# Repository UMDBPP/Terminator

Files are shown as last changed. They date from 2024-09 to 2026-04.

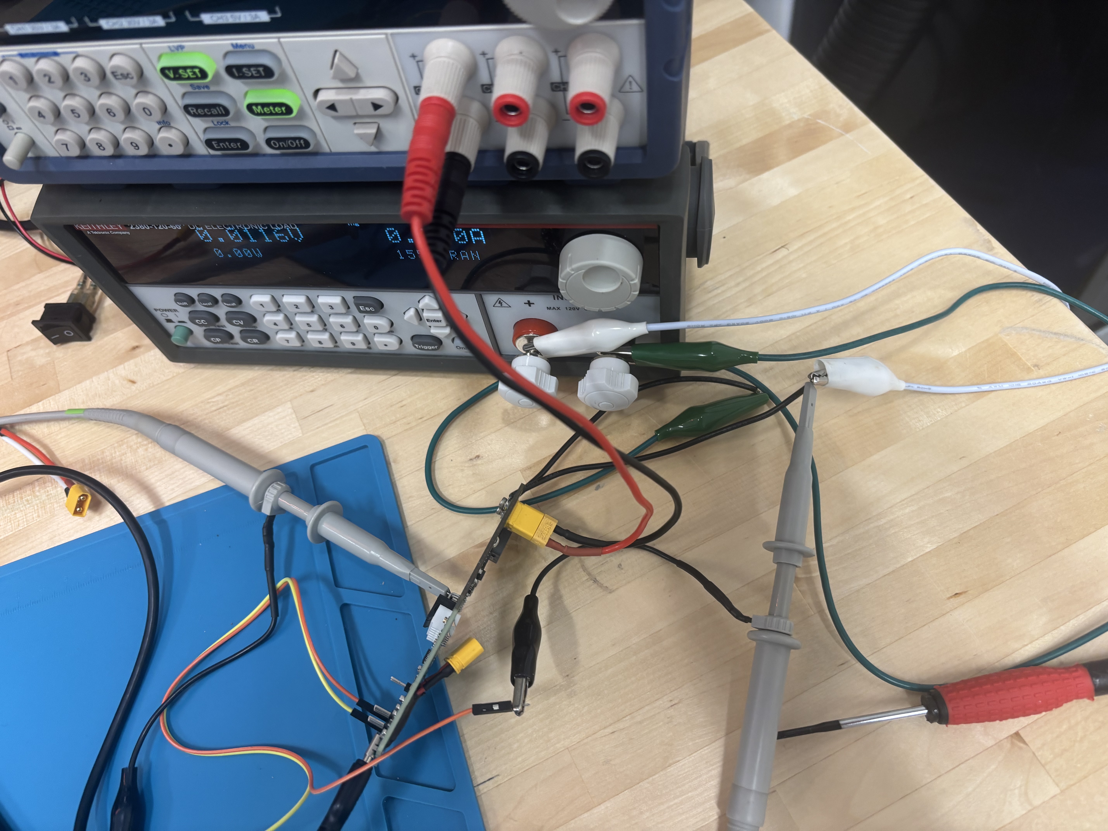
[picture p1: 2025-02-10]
Testing/T100x/TW_Load_Step/IMG_1361.jpeg

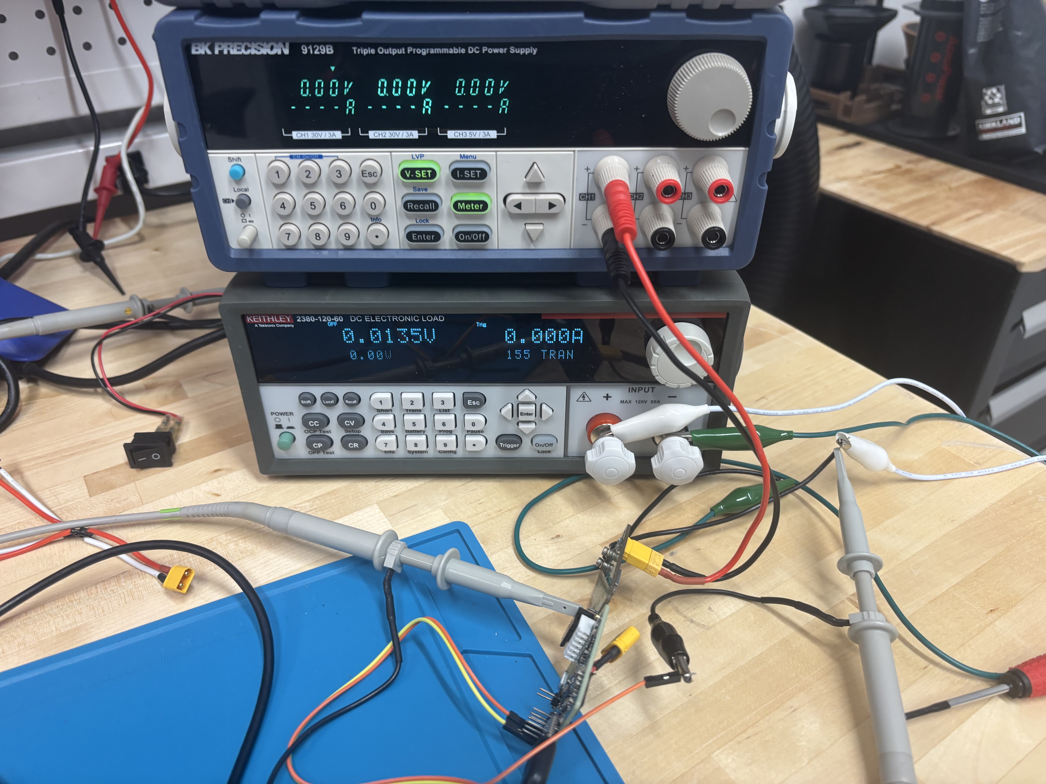
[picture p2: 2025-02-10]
Testing/T100x/TW_Load_Step/IMG_1360.jpeg

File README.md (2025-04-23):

# Terminator
A flight termination device for BPP.

## `T1100` - Current Revision

Much the same as T1000 but simpler and more complete.

## `T1000`
Shipman's ENEE499L project. The digital portion integrates a STM32L4, GPS, P/T Sensor, FRAM, and SX1262 Radio. This should provide quite a bit of flexibility in a small package while consuming minimal power. The digital board interfaces with a cutdown board which performs hot-wire termination like many other designs. However, this board is really just a barebones buck converter power stage that will be controlled by the digital board. This should provide increased flexiblity and efficiency over other implementations while also allowing T1000 to terminate even 550 paracord.

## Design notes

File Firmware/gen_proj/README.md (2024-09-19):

This project was originally generated by the STM32 Cube IDE. I just stole it and rippped it apart so I could build it myself and not be forced to use their IDE. Hopefully I'll also be able to steal some of their HAL functions too since I don't want to have to write them myself. The original project I used can be found in "empty_test_proj.zip"

# Project Structure
The structure of the project isn't too complicated.
- **build**: this fold contains the makefile and linker script used to build the final .elf file and other artifacts created during a build
- **src**: this contains source files that YOU write, things like main.c and other small or libraries
- **lib**: this is where you should put libraries you need to use for things like accessing I2C devices or parsing GPS data
- **vendor**: this includes code written by ARM and ST which perform basic configuration functions (e.g. the basic assembly run by the processor at startup that puts your application code in the right place in memory), unless you know what you are doing in here don't touch
    - **CMSIS**: this is the core stuff that configures the processor
    - **STM32L4_HAL**: this is hardware abstraction layer code written by ST, it should make things like using ADCs and configuring GPIOs easier, it is documented in ST UM1884 (google it)

## External Software Versions
ARM CMSIS, ST CMSIS, and the STM32 HAL found in the vendor directory are all external software provided by vendors. As described here: https://htmlpreview.github.io/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, they need to have the correct versions installed to function properly.

These version numbers are denoted by the release tags shown in Git or on the Github website and it's very easy to move between versions.

1. First check the versions you need by going to the link above and scrolling down to `Components > Drivers`
2. `cd` into `Terminator/Firmware/gen_proj/vendor/CMSIS`
3. List all available tags using `git tag`
4. Switch to the tag corresponding to the desired version number with `git checkout tags/<tag> -b <branch>`
    - Where `<tag>` is probably something like `5.6.0` and `<branch>` is probably `main`
5. Then confirm which tag you are on with `git describe --exact-match --tags`
6. Repeat steps 3-5 but first `cd Terminator/Firmware/gen_proj/vendor/CMSIS/Device/ST/STM32L4`
7. Repeat steps 3-5 but first `cd Terminator/Firmware/gen_proj/vendor/STM32L4_HAL`

# Building
The `build` folder is where the magic happens. The critical things it contains are: 

- **`makefile`**: contains the "recipe" for compiling code and creating an executable
- **`*.elf`**: the final executable, this is loaded onto a microcontroller and run
- **linker script**: a file that tells the linker where to put code in memory so that it will run properly

The TLDR steps for just building and flashing something are this:
1. `cd build` and run `make`
2. If you are connected to the MCU with an ST Link or some other programmer/debugger that is OpenOCD compatible, run `make flash`
3. If you are just connected over USB, but the device in USB DFU mode and flash the `.elf` file found in `build` to the device using the STM32 Programmer application

# References
Things I used to figure this out.
- ENEE440 - great class IMO, but I'm really into all this stuff so YMMV
- https://kleinembedded.com/stm32-without-cubeide-part-1-the-bare-necessities/
    - this really does explain most of it quite nicely, I had to figure some things out on my own to get this approach working with ST's provided startup and linker scripts
- https://vivonomicon.com/2018/04/02/bare-metal-stm32-programming-part-1-hello-arm/
- https://gist.github.com/maxtruxa/4b3929e118914ccef057f8a05c614b0f for the original Makefile

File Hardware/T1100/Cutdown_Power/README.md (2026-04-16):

Cutdown power stage for T1000 nichrome. [Click here to view in browser.](https://kicanvas.org/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)

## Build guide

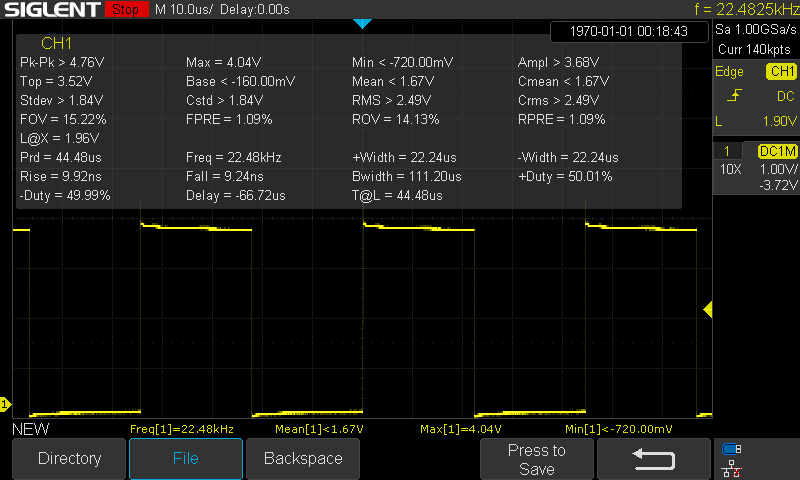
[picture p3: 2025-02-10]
Testing/T100x/TW_Load_Step/pid_loop_time.png

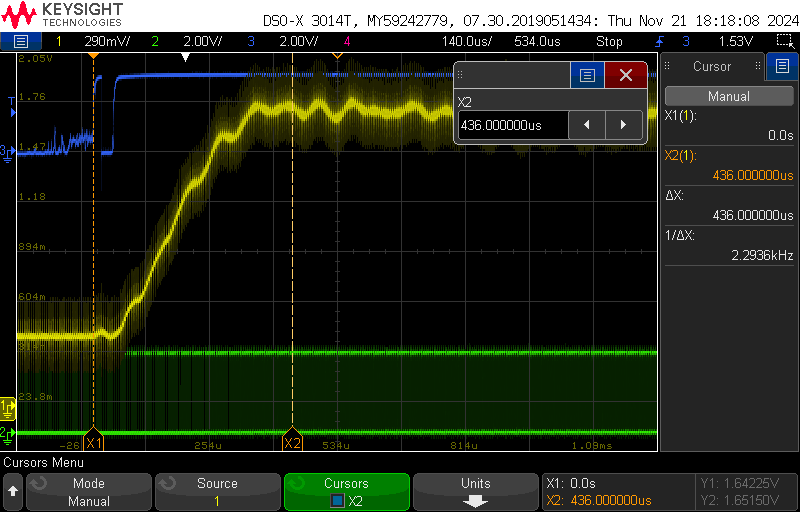
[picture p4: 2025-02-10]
Testing/T100x/TW_Load_Step/scope_4.png

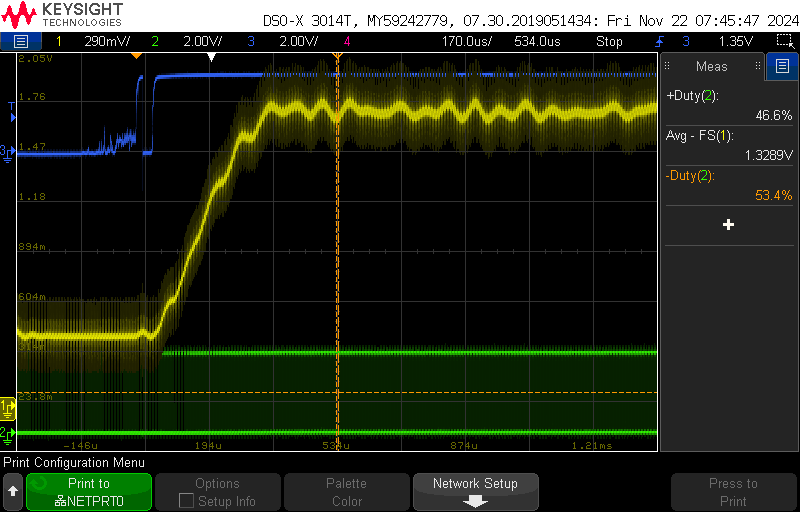
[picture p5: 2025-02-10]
Testing/T100x/TW_Load_Step/scope_0.png

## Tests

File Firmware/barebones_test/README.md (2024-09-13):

This directory is meant for developing the barebones components necessary to build a STM32 project from scratch. The two tutorials below have some good info. At some point I'd like to do this, but for now I can just copy a project generated by the STM32 Cube IDE and build it myself, which is easier since it generates all of the necessar boilerplate for me.

https://vivonomicon.com/2018/04/02/bare-metal-stm32-programming-part-1-hello-arm/
https://kleinembedded.com/stm32-without-cubeide-part-1-the-bare-necessities/

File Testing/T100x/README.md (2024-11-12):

# T100x Testing
A collection of data from testing T100x iterations. See the wiki development logs for more commentary.

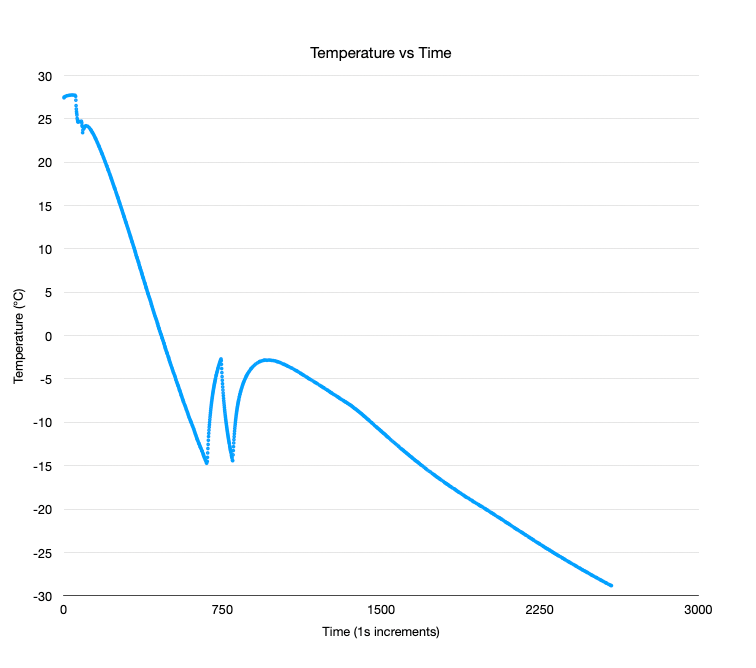
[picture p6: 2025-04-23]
Testing/T1100/T1100_board_heater_test_04212025.png

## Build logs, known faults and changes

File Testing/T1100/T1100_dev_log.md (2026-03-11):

# Board Heater

## Test 1

Ok so the little thermo-couple thermostat thing I chose works great. Turns on and off the NMOS FET perfectly and the long trace embeded in the board is very clearly able to heat it. The data in the 04/21/2025 graph shows that the heater brought the temp up from -15 C twice and then seemed to give up? That or it looks like it was just continuously on since the cooling happened much slower.

It only ran for ~43 minutes from what I can tell and restarted a lot once it reached about -28 C. The battery is also not very discharged so I'm not surprised that it didn't run very long. I'm going to re-run this test and log board temperature as well. My only other thought is that the battery got too cold for the amount of current the board heater draws so the system started dropping out. Not sure the best way to go about attaching the battery to the board since the back needs to be open for flight line to pass over.

Additionally since the system runs at 3.3V, maybe a 2S LiPo would be a better fit. Options are:
1. https://hobbyking.com/en_us/turnigy-nano-tech-300mah-2s-35c-lipo-pack-w-jst-ph-connector.html
2. https://hobbyking.com/en_us/turnigy-nano-tech-450mah-2s-65c-lipo-e-flite-compatible-blade-130x-eflb3002s35.html

## Test 2

This time also only ran for ~42 minutes which is odd to me, perhaps just a coincidence. This time I doubled the power through the heater and it worked much better before I'm pretty sure the battery voltage dropped to 3.3-3.4V and the regulator started having difficulties.

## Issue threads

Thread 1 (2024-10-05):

DIP Switch Pin out incorrect

michaelshipman, 2024-10-05:
Pin numbers and physical connections do not agree, currently bodging

michaelshipman, 2024-10-31:
Fixed on T1001

Closed 2024-10-31.

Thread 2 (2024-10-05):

GPS footprint pin 1 marking missing

michaelshipman, 2024-10-05:
need to add

Closed 2024-10-08.

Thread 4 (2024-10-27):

GPS Not working on battery power

michaelshipman, 2024-10-27:
For some reason the M10s have a VIO select option that either needs to be open or grounded depending on if 3.3v or 1.8v is used, either need to make system always use ~3v or implement some kind of solution

michaelshipman, 2024-10-31:
Fix for the moment is bumping the battery supplied regulator up to ~3.25v

michaelshipman, 2024-11-01:
New resistor values calculated, battery reg should be at a little under 3v once these come in.
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

Closed 2024-11-01.

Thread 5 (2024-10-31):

GPS returning incorrect coordinates and long lock time

michaelshipman, 2024-10-31:
Will have to put in actual numbers later but the coordinates from the receiver are pretty wrong, still in Maryland but probably 30ish miles away. UTC time is correct though.

I'm not sure why this is the case given that it was working a week or two ago.

Coupled with this issue is 20+ minute lock times for position.

I think my best bet right now is to reseat the GPS receiver, maybe over the last few weeks and a launch a solder joint or two have partially failed.

michaelshipman, 2024-11-01:
Replaced the MIA (from rev 0 build) and the antenna (new) and left running for a bit on the picnic table outside of MFG, not sure how long but I don't think more than 15 minutes.

Got time again but nothing else.

michaelshipman, 2024-11-01:
Going to put the RTC crystal on, RTC_O is supposed to be grounded when not used so I wonder if it's causing EMI issues

michaelshipman, 2024-11-01:
also the trace width was 0.22mm and JLC says it should be 0.1565, kicad calculator says 0.2

michaelshipman, 2024-11-01:
Viewing the spectrum, it's not the worst I've seen but not like the nice pretty one in the ublox manual. I'm not sure what the spikes are for one thing. It seems like a decently well formed spectrum and considering I'm in my apartment next to the window the received signal strength doesn't seem unrealistic.

**For future reference: the UBX-MON-SPAN is in View > Messages > Scroll down to Mon**

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

michaelshipman, 2024-11-01:
Oh also GPS baud for the MIA is 38400

michaelshipman, 2024-11-12:
I revved the board to T1002 to tune up the GPS section, have not assembled or tested yet but tuned the antenna line impedance and improved grounding

michaelshipman, 2024-11-14:
So I'm a bit of a dumb dumb, the NMEA lat long format confused me a little bit

This is what I got when the GPS did eventually get lock: 3859.55949,N,7656.33880,W

This is actually 38 + (59.55949 / 60) = 38.9926581667, and -76 + (56.33880 / 60) = -76.93898

Which is right on MFG actually

I still can't get it to lock consistently or quickly, but it does actually work when it does get position fix

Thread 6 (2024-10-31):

MS5607 I2C Inconsistent I2C comms

michaelshipman, 2024-10-31:
Some times data is just not being received. Unsure if this is a failure to wait for the device to fully convert/parse commands or something else. Tried lowering pull ups to 6.81k which didn't seem to help.

Sometimes data is returned though. Not entirely sure if it's correct data yet. May need to try and find a new one and see if this one is a dud.

Confident in the solder joints.

michaelshipman, 2024-11-12:
I added 20ms delays after transmitting commands and it's working nicely now. Have not tried to tune to shorter delay yet since it's not top priority before NS-130

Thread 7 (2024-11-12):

Re-assign exposed pins so USART TX/RX available on header

michaelshipman, 2024-11-12:
If possible try to re-assign exposed pins so that USART TX/RX can be used while cutdown power stage is attached. Can dump data over TX right now if re-assign PA2 which is used for power stage current sense.

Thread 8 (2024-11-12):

Power stage LVC/shutdown signal

michaelshipman, 2024-11-12:
The digital system should be able to power off the power stage board to save on power when not using it to cut. 1mA continuous draw adds up over the course of hours so being able to shut off the boost regulator on board would cut down on that.

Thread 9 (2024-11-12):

Move nichrome mount points on cutdown power stage

michaelshipman, 2024-11-12:
At the very least they need to be further apart to allow 550 paracord to fit between them.

More generally the physical layout of system needs to be improved since you can't package it the way I want to right now. This was partially intentional since the focus so far has been on designing something that could be tested and working with easily. But it means that it can't be packaged right now.

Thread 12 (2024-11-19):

GPS IO Voltage Switch

michaelshipman, 2024-11-19:
Need to select 1.8V or 3.3V on the MIA, added NMOS switched by OR controller that should solve this

Closed 2024-11-19.

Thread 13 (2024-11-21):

Interrupts not working on battery

michaelshipman, 2024-11-21:
I'm pretty sure this is the case for some reason, need to check on it again

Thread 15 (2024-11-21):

calculate LVC resistors for digital board reg

michaelshipman, 2024-11-21:
idk how I keep getting it wrong but it cuts off at 2.8V right now

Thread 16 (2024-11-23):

Swap STM32 HSE with a 32 MHz (or other) source

michaelshipman, 2024-11-23:
25 MHz doesn't divide evenly down to 48MHz which makes it impossible to use USB and have the core clock > the HSE source. 32 MHz or some other speed would be better, the TCXO used for the SX1262 should be pin to pin compatible with the current HSE, not sure if the footprint is close enough

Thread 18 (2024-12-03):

Potential Crosstalk on Digital Board

michaelshipman, 2024-12-03:
I haven't observed any issues but this was a silly oversight

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

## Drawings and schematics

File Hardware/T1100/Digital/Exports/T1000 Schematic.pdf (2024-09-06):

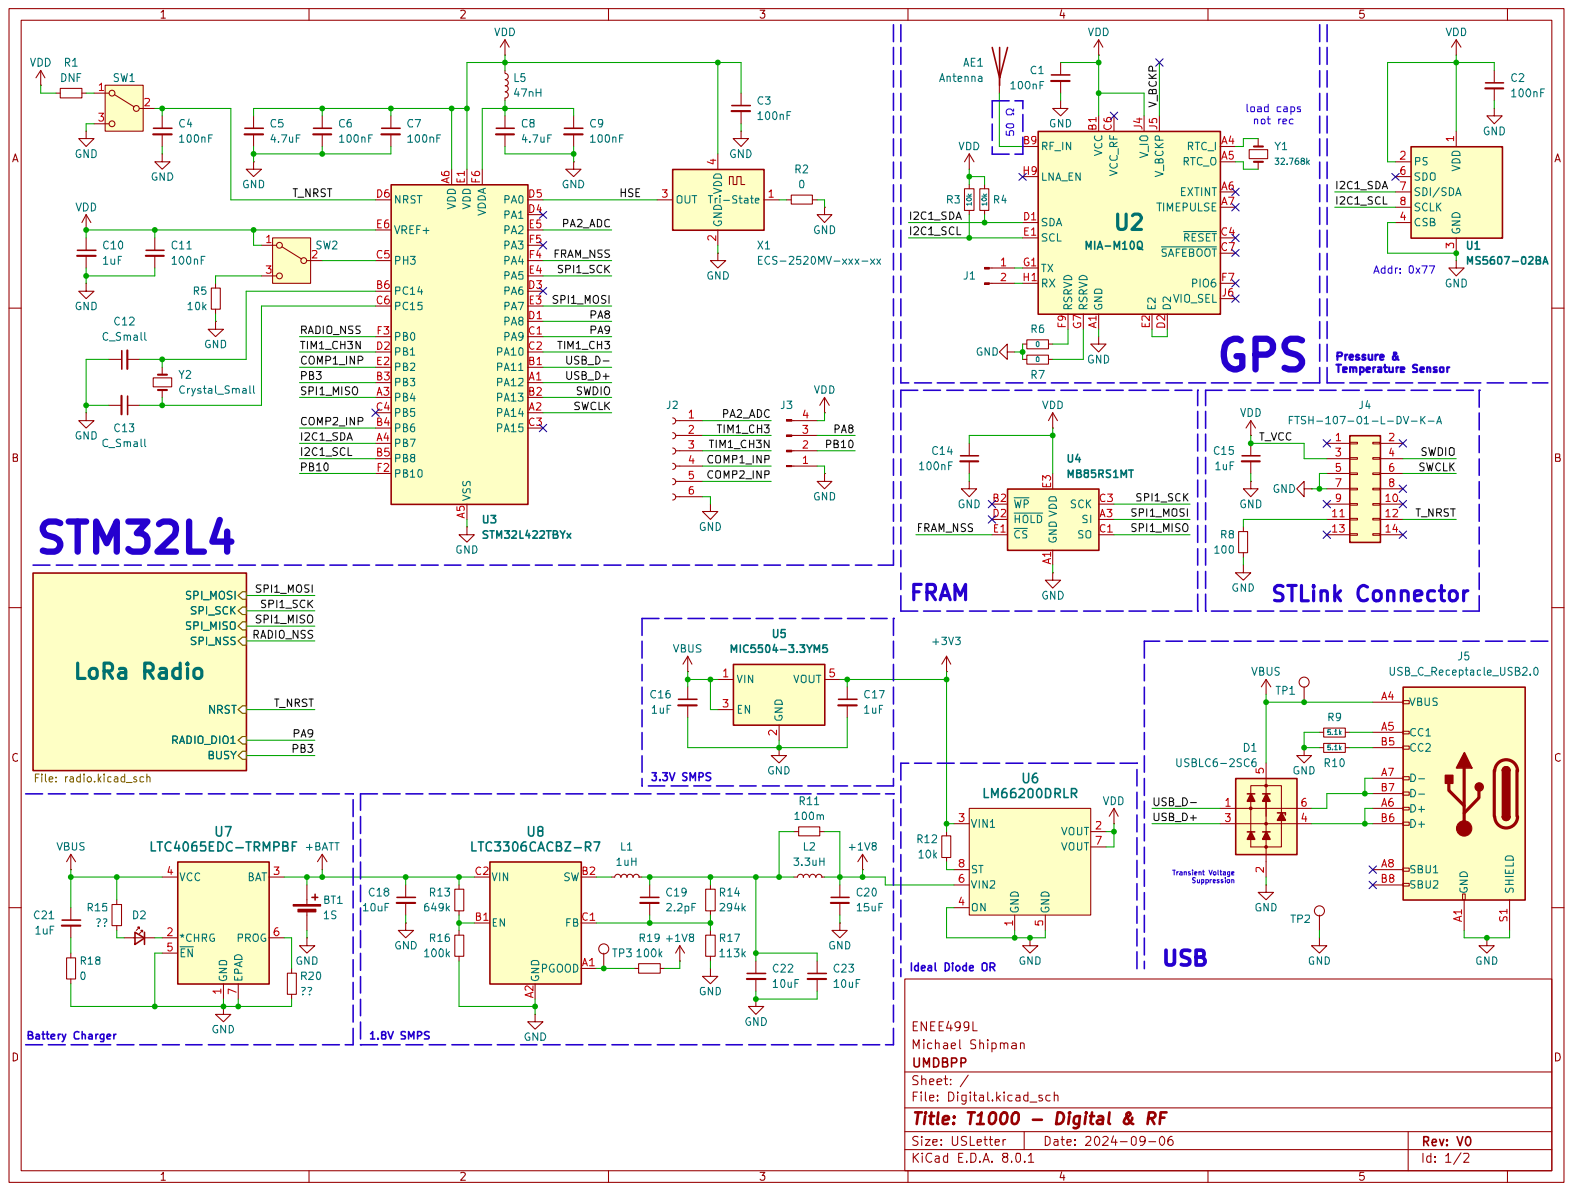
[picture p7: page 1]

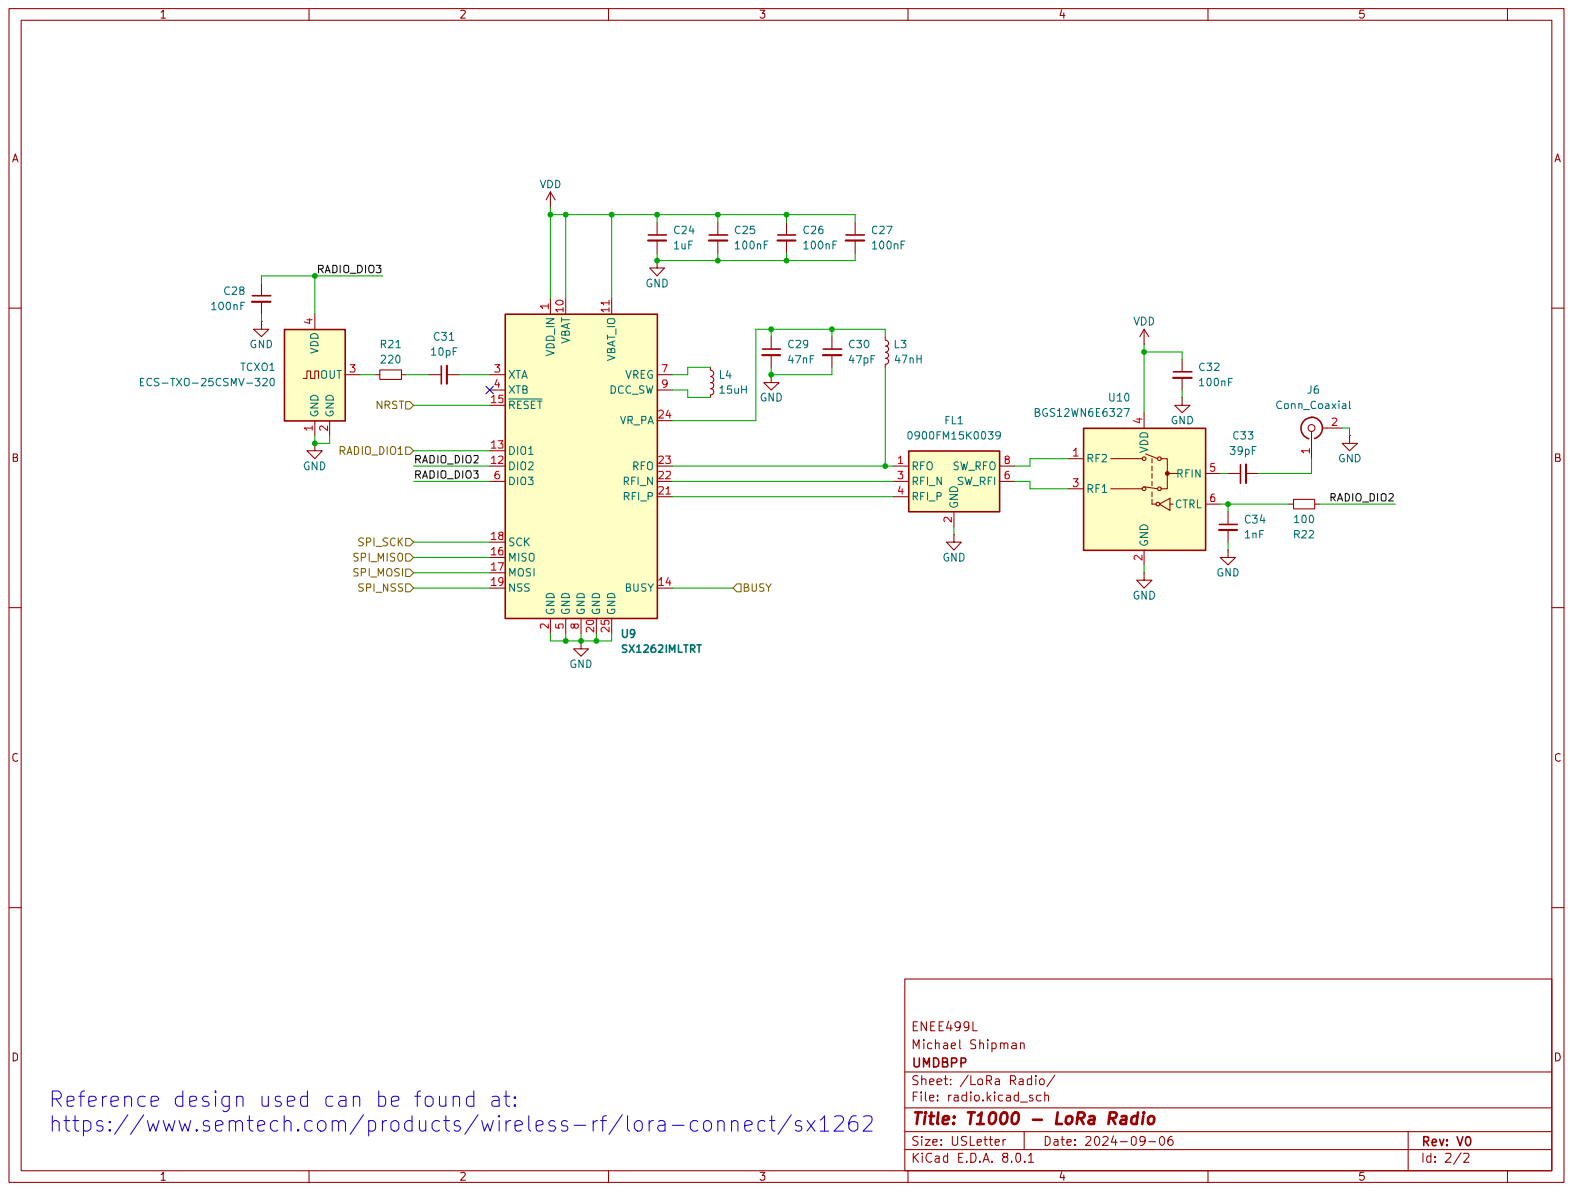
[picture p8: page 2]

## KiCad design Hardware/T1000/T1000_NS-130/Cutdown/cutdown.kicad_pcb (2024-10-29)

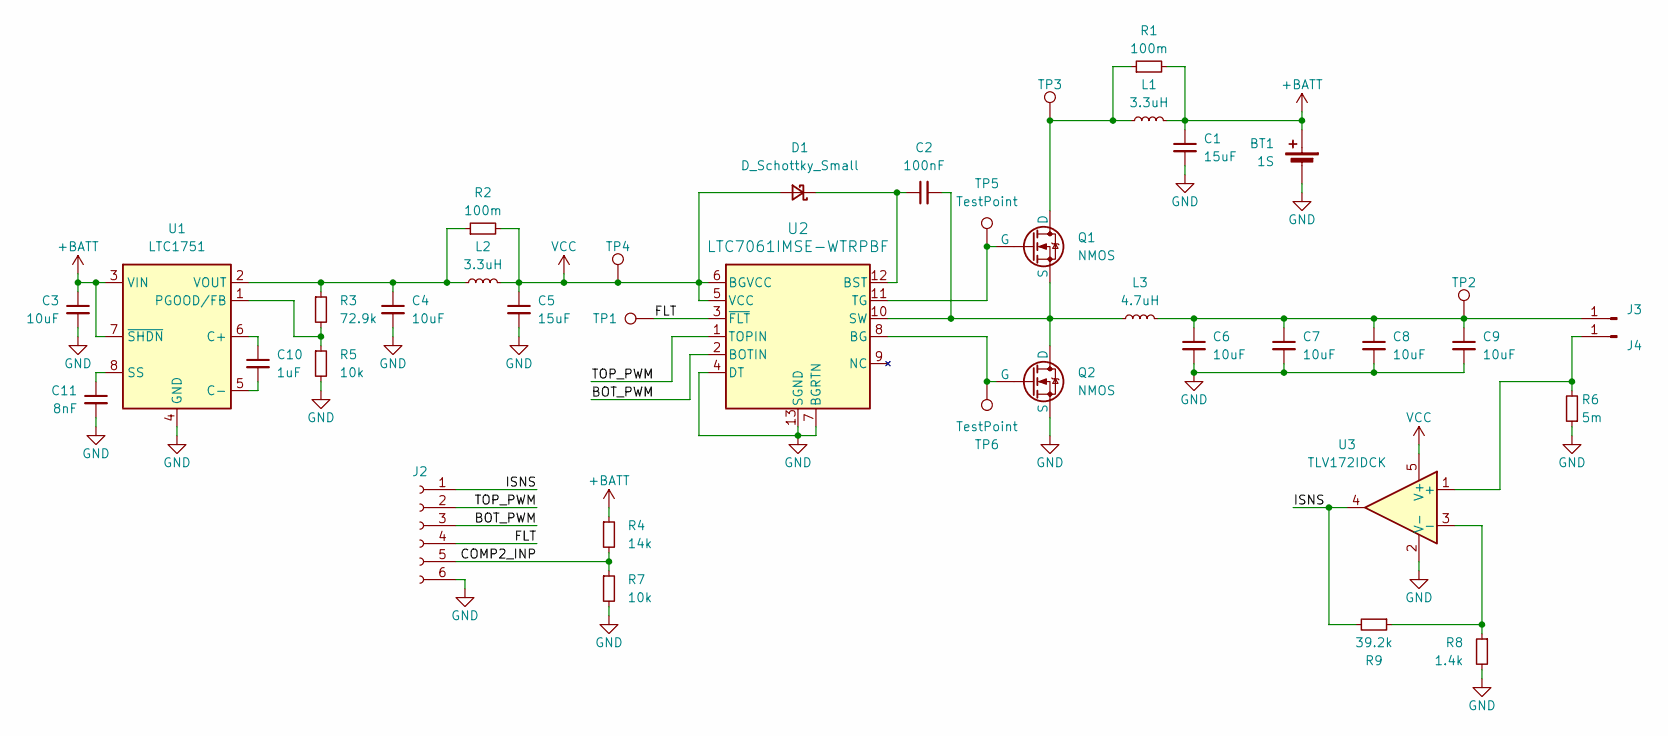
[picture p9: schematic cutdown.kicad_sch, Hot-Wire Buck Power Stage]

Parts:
BT1: 1S; AMASS_XT30U-F_1x02_P5.0mm_Vertical
C1, C5: 15uF; C_1206_3216Metric
C2: 100nF; C_0603_1608Metric
C3, C4: 10uF; C_0805_2012Metric
C6, C7, C8, C9: 10uF; C_1206_3216Metric
C10: 1uF; C_0603_1608Metric
C11: 8nF; C_0603_1608Metric
D1: D_Schottky_Small; D_SMA
J2: Conn_01x06_Socket; PinHeader_1x06_P2.54mm_Vertical
J3, J4: Conn_01x01_Pin; MountingHole_2.2mm_M2_DIN965_Pad
L1, L2: 3.3uH; L_1210_3225Metric
L3: 4.7uH; Wurth_74437368047
Q1, Q2: NMOS; CSD17307Q5A
R1, R2: 100m; C_0603_1608Metric
R3: 72.9k; R_0402_1005Metric
R4: 14k; R_0402_1005Metric
R5, R7: 10k; R_0402_1005Metric
R6: 5m; R_2512_6332Metric
R8: 1.4k; R_0603_1608Metric_Pad0.98x0.95mm_HandSolder
R9: 39.2k; R_0603_1608Metric_Pad0.98x0.95mm_HandSolder
TP1, TP2, TP3, TP4: TestPoint; TestPoint_Keystone_5000-5004_Miniature
TP5, TP6: TestPoint; TestPoint_Pad_D1.0mm
U1: LTC1751; MSOP-8_3x3mm_P0.65mm
U2: LTC7061IMSE-WTRPBF; MSOP-12-1EP_3x4mm_P0.65mm_EP1.65x2.85mm
U3: TLV172IDCK; SOT-353_SC-70-5

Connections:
+BATT: BT1.2 (+), C1.1, C3.1, L1.2, R1.2, R4.1, U1.3 (VIN), U1.7 (~SHDN)
/BOT_PWM: J2.3, U2.2 (BOTIN)
/COMP2_INP: J2.5, R4.2, R7.1
/FLT: J2.4, TP1.1, U2.3 (~FLT)
/ISNS: J2.1, R9.2, U3.4
/TOP_PWM: J2.2, U2.1 (TOPIN)
GND: BT1.1 (-), C1.2, C3.2, C4.2, C5.2, C6.2, C7.2, C8.2, C9.2, C11.2, J2.6, Q2.3 (S), R5.2, R6.1, R7.2, R8.2, U1.4 (GND), U2.4 (DT), U2.7 (BGRTN), U2.13 (SGND), U3.2 (V-)
unnamed: C2.1, D1.1 (K), U2.12 (BST)
unnamed: C6.1, C7.1, C8.1, C9.1, J3.1, L3.2, TP2.1
unnamed: J4.1, R6.2, U3.1 (+)
unnamed: L1.1, Q1.1 (D), R1.1, TP3.1
unnamed: Q1.2 (G), TP5.1, U2.11 (TG)
unnamed: C2.2, L3.1, Q1.3 (S), Q2.1 (D), U2.10 (SW)
unnamed: Q2.2 (G), TP6.1, U2.8 (BG)
unnamed: C10.1, U1.6 (C+)
unnamed: C10.2, U1.5 (C-)
unnamed: R3.2, R5.1, U1.1 (PGOOD/FB)
unnamed: C11.1, U1.8 (SS)
unnamed: C4.1, L2.1, R2.1, R3.1, U1.2 (VOUT)
unnamed: R8.1, R9.1, U3.3 (-)
VCC: C5.1, D1.2 (A), L2.2, R2.2, TP4.1, U2.5 (VCC), U2.6 (BGVCC), U3.5 (V+)

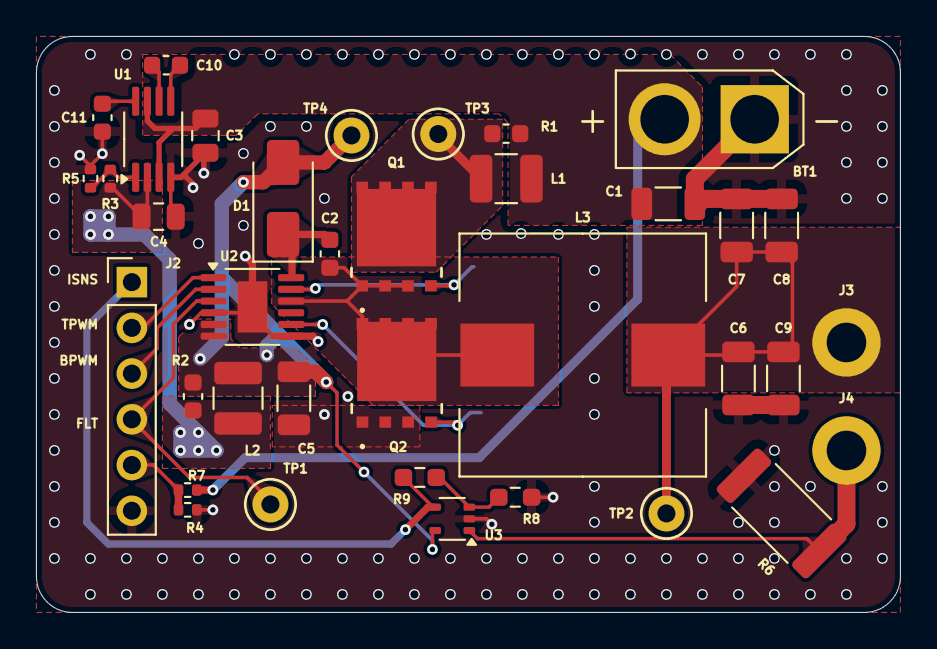
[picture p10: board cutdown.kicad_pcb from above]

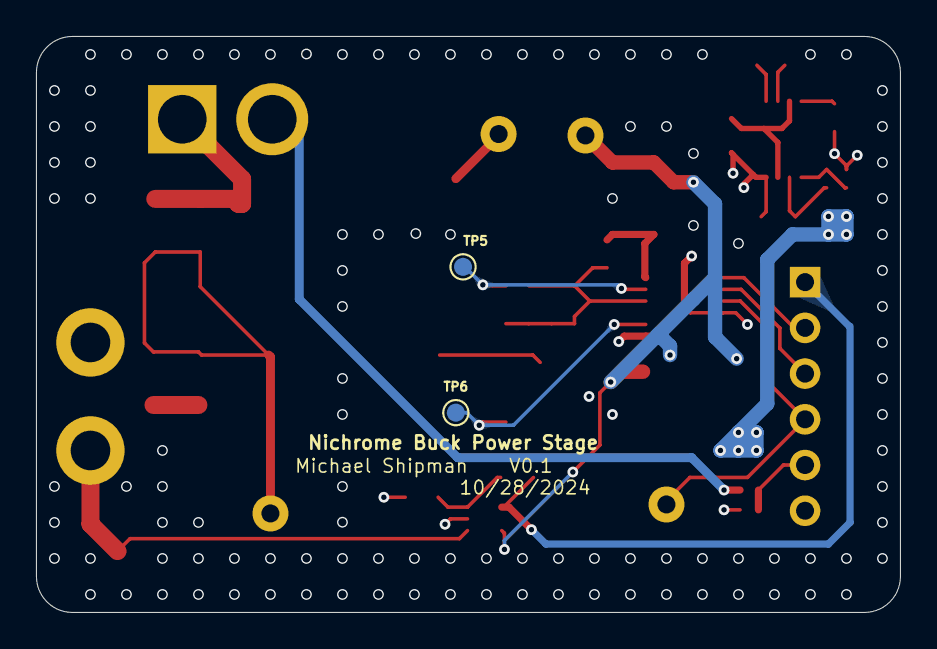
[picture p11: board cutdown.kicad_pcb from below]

Board: 4 copper layers, 48.0 x 32.0 mm, 39 parts (2 on the bottom side), 21 nets.

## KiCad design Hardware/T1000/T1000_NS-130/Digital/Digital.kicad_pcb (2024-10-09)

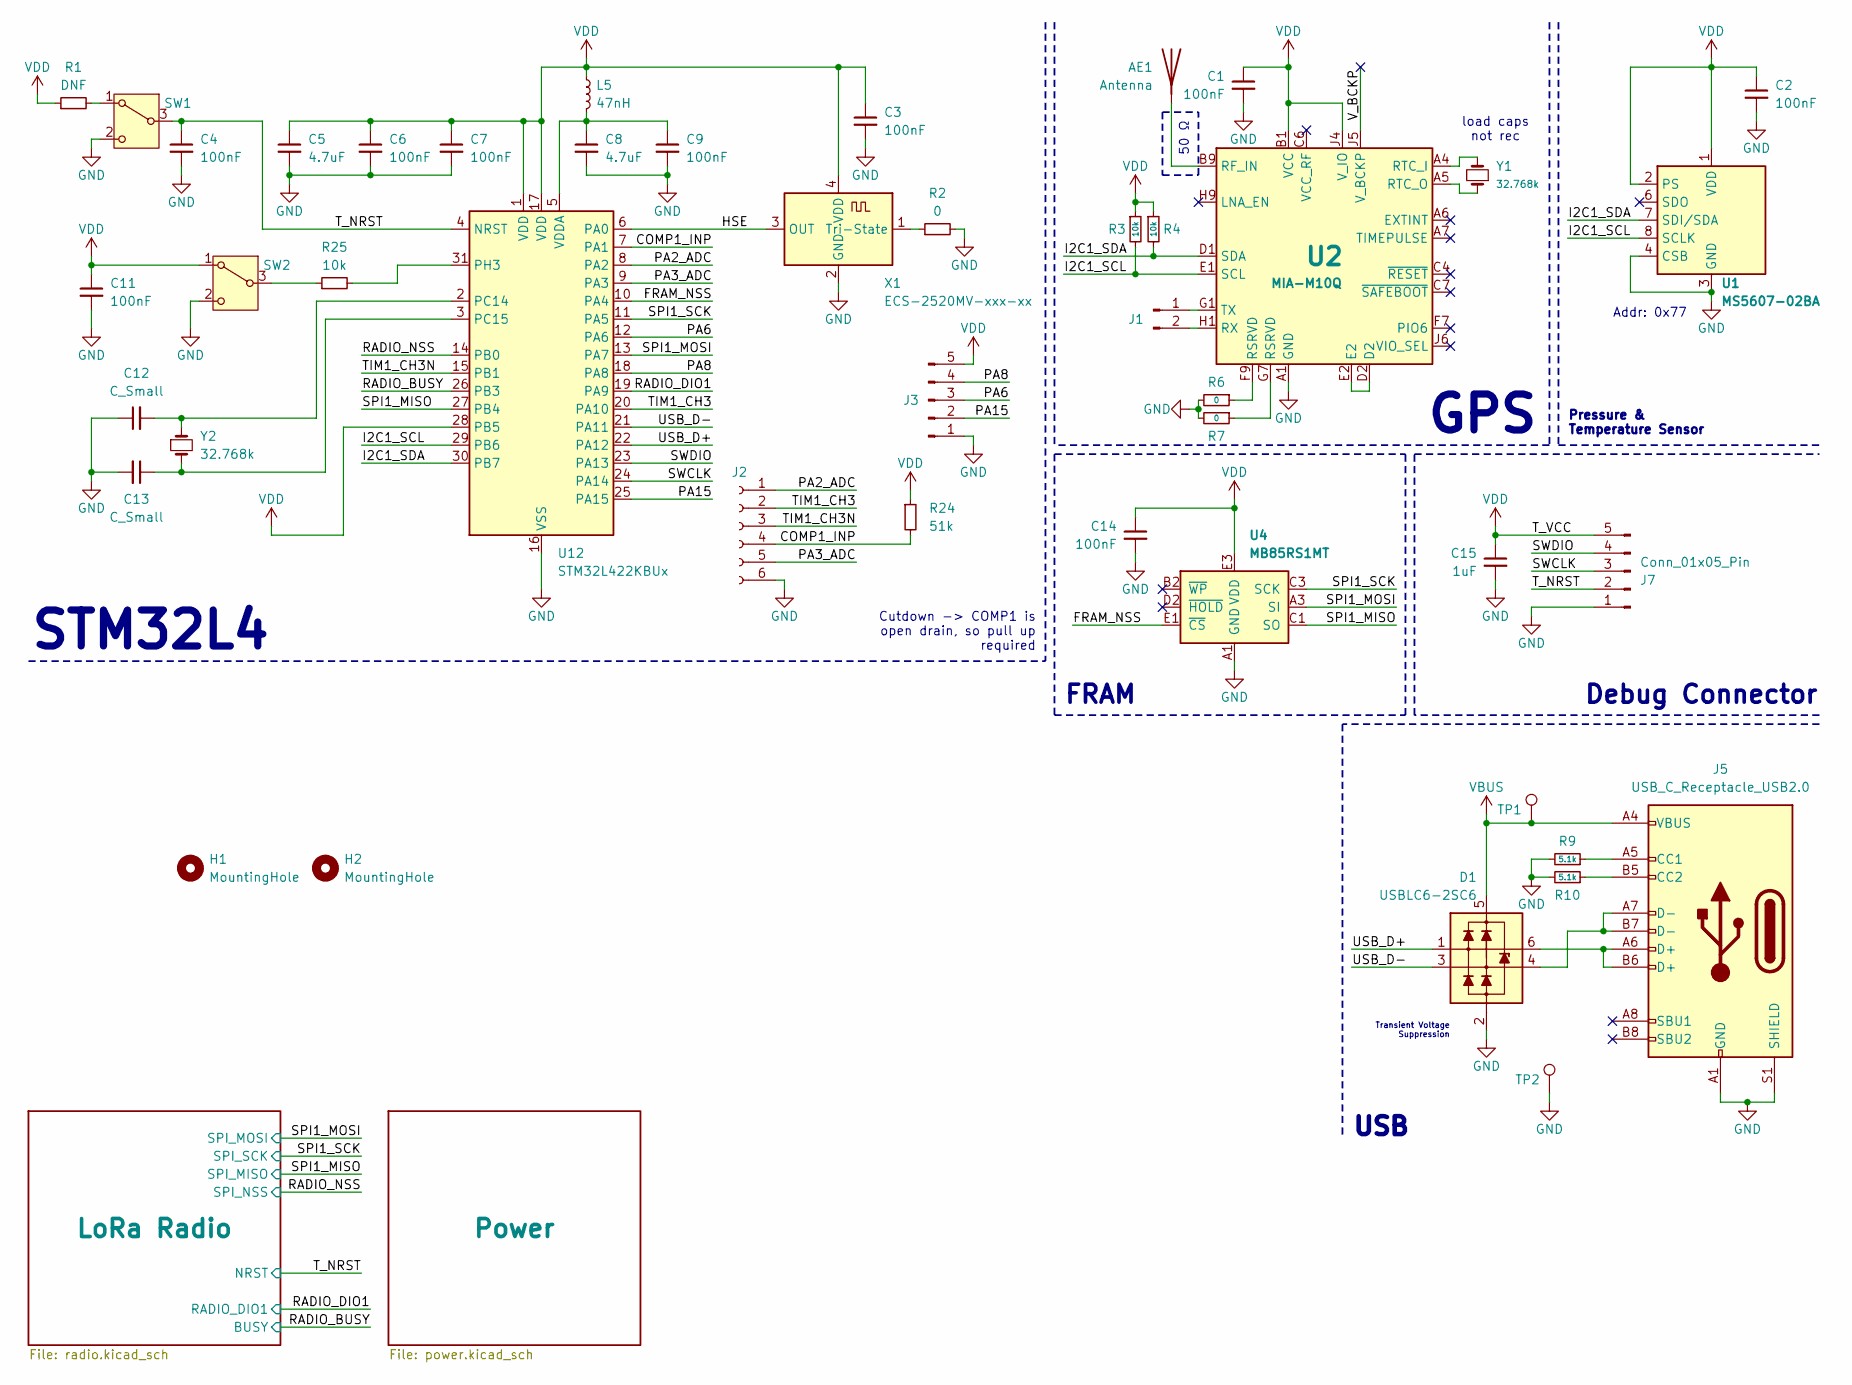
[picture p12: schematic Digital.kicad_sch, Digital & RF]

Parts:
AE1: Antenna; ANT_1575AT_JOT-M
C1, C2, C3, C4, C6, C7, C9, C11, C14: 100nF; C_0402_1005Metric
C5, C8: 4.7uF; C_0603_1608Metric
C12, C13: C_Small; C_0402_1005Metric
C15: 1uF; C_0603_1608Metric
D1: USBLC6-2SC6; TSOT-23-6
H1, H2: MountingHole; MountingHole_2.2mm_M2
J1: Conn_01x02_Pin; PinHeader_1x02_P2.54mm_Vertical
J2: Conn_01x06_Socket; PinHeader_1x06_P2.54mm_Vertical
J3, J7: Conn_01x05_Pin; PinHeader_1x05_P2.54mm_Vertical
J5: USB_C_Receptacle_USB2.0; USB_C_Receptacle_GCT_USB4105-xx-A_16P_TopMnt_Horizontal
L5: 47nH; L_0402_1005Metric
R1: DNF; R_0402_1005Metric
R2, R6, R7: 0; R_0402_1005Metric
R3, R4, R25: 10k; R_0402_1005Metric
R9, R10: 5.1k; R_0402_1005Metric
R24: 51k; R_0402_1005Metric
SW1, SW2: SW_SPDT; CAS-120TB_NDC-M
TP1, TP2: TestPoint; TestPoint_Pad_D1.0mm
U1: MS5607-02BA; LGA-8_3x5mm_P1.25mm
U2: MIA-M10Q
U4: MB85RS1MT; BGA8CP30X40_5X3_309X228X35B25N
U12: STM32L422KBUx; QFN-32-1EP_5x5mm_P0.5mm_EP3.45x3.45mm
X1: ECS-2520MV-xxx-xx; Oscillator_SMD_ECS_2520MV-xxx-xx-4Pin_2.5x2.0mm
Y1, Y2: 32.768k; Crystal_SMD_3215-2Pin_3.2x1.5mm

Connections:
/COMP1_INP: J2.4, R24.2, U12.7 (PA1)
/FRAM_NSS: U4.E1 (~CS), U12.10 (PA4)
/HSE: U12.6 (PA0), X1.3 (OUT)
/I2C1_SCL: R3.2, U1.8 (SCLK), U2.E1 (SCL), U12.29 (PB6)
/I2C1_SDA: R4.2, U1.7 (SDI/SDA), U2.D1 (SDA), U12.30 (PB7)
/PA2_ADC: J2.1, U12.8 (PA2)
/PA3_ADC: J2.5, U12.9 (PA3)
/PA6: J3.3, U12.12 (PA6)
/PA8: J3.4, U12.18 (PA8)
/PA15: J3.2, U12.25 (PA15)
/RADIO_BUSY: U12.26 (PB3); also elsewhere on the board
/RADIO_DIO1: U12.19 (PA9); also elsewhere on the board
/RADIO_NSS: U12.14 (PB0); also elsewhere on the board
/SPI1_MISO: U4.C1 (SO), U12.27 (PB4); also elsewhere on the board
/SPI1_MOSI: U4.A3 (SI), U12.13 (PA7); also elsewhere on the board
/SPI1_SCK: U4.C3 (SCK), U12.11 (PA5); also elsewhere on the board
/SWCLK: J7.3, U12.24 (PA14)
/SWDIO: J7.4, U12.23 (PA13)
/TIM1_CH3: J2.2, U12.20 (PA10)
/TIM1_CH3N: J2.3, U12.15 (PB1)
/T_NRST: C4.1, J7.2, SW1.3 (C), U12.4 (NRST); also elsewhere on the board
/USB_D+: D1.1 (L1), U12.22 (PA12)
/USB_D-: D1.3 (L2), U12.21 (PA11)
/V_BCKP: U2.J5 (V_BCKP)
GND: C1.2, C2.2, C3.2, C4.2, C5.2, C6.2, C7.2, C8.2, C9.2, C11.2, C12.1, C13.2, C14.2, C15.2, D1.2 (VN), J2.6, J3.1, J5.A1 (GND), J5.A12 (GND), J5.B1 (GND), J5.B12 (GND), J5.S1 (SHIELD), J7.1, R2.2, R6.2, R7.2, R9.2, R10.2, SW1.2 (B), SW2.2 (B), TP2.1, U1.3 (GND), U1.4 (CSB), U1.5 (CSB), U2.A1 (GND), U2.A2 (GND), U2.A3 (GND), U2.A8 (GND), U2.A9 (GND), U2.B2 (GND), U2.B8 (GND), U2.C3 (GND), U2.C9 (GND), U2.E3 (GND), U2.E4 (GND), U2.E9 (GND), U2.F1 (GND), U2.F3 (GND), U2.F4 (GND), U2.G3 (GND), U2.G4 (GND), U2.G5 (GND), U2.G6 (GND), U2.H8 (GND), U2.J8 (GND), U2.J9 (GND), U4.A1 (GND), U12.16 (VSS), U12.32 (VSS), U12.33 (VSS), X1.2 (GND); also elsewhere on the board
unnamed: AE1.1 (A), U2.B9 (RF_IN)
unnamed: D1.6 (L1), J5.A6 (D+), J5.B6 (D+)
unnamed: D1.4 (L2), J5.A7 (D-), J5.B7 (D-)
unnamed: J1.1, U2.G1 (TX)
unnamed: J1.2, U2.H1 (RX)
unnamed: J5.A5 (CC1), R9.1
unnamed: J5.B5 (CC2), R10.1
unnamed: R6.1, U2.F9 (RSRVD)
unnamed: R7.1, U2.G7 (RSRVD)
unnamed: R1.2, SW1.1 (A)
unnamed: R25.1, SW2.3 (C)
unnamed: U2.A4 (RTC_I), Y1.2
unnamed: U2.A5 (RTC_O), Y1.1
unnamed: C12.2, U12.2 (PC14), Y2.1
unnamed: C13.1, U12.3 (PC15), Y2.2
unnamed: R25.2, U12.31 (PH3)
unnamed: C8.1, C9.1, L5.2, U12.5 (VDDA)
unnamed: R2.1, X1.1 (Tri-State)
VBUS: D1.5 (VP), J5.A4 (VBUS), J5.A9 (VBUS), J5.B4 (VBUS), J5.B9 (VBUS), TP1.1; also elsewhere on the board
VDD: C1.1, C2.1, C3.1, C5.1, C6.1, C7.1, C11.1, C14.1, C15.1, J3.5, J7.5, L5.1, R1.1, R3.1, R4.1, R24.1, SW2.1 (A), U1.1 (VDD), U1.2 (PS), U2.B1 (VCC), U2.J4 (V_IO), U4.E3 (VDD), U12.1 (VDD), U12.17 (VDD), U12.28 (PB5), X1.4 (VDD); also elsewhere on the board

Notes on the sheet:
load caps not rec
GPS
Transient Voltage Suppression
Debug Connector
Cutdown -> COMP1 is open drain, so pull up required
FRAM
50 Ω
USB
Pressure & Temperature Sensor
STM32L4
Addr: 0x77

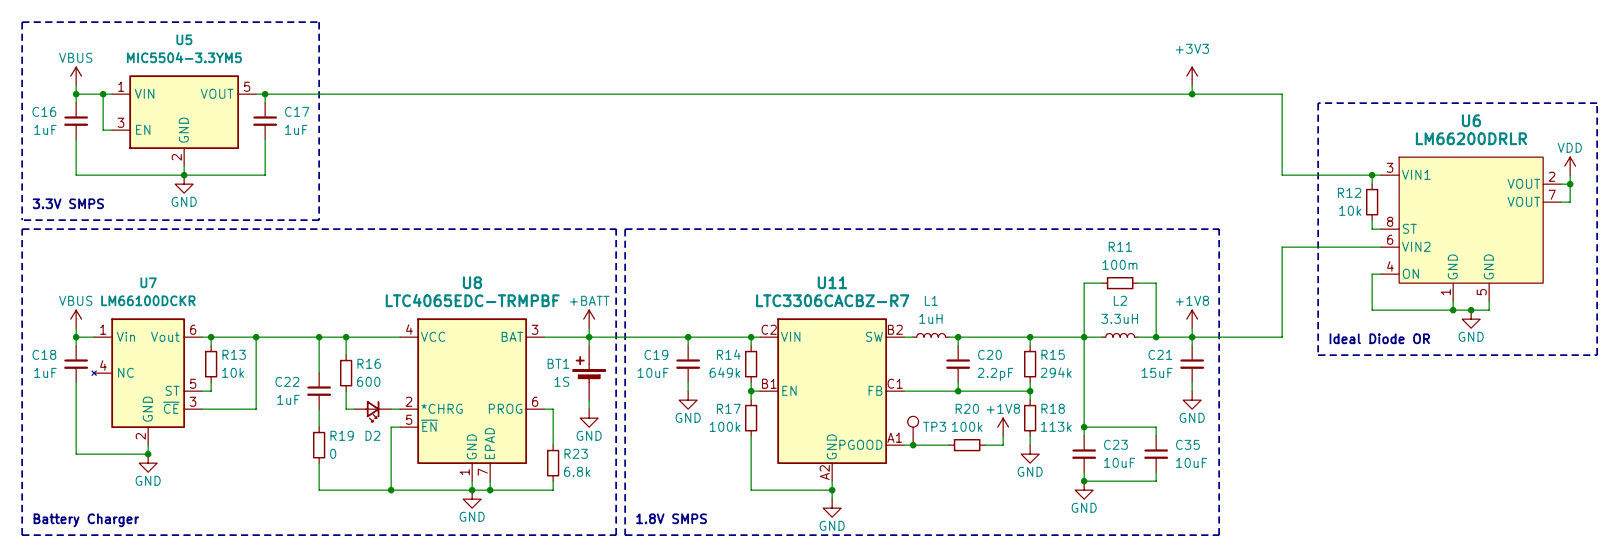
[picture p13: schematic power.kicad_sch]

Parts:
BT1: 1S; PinHeader_1x02_P2.54mm_Vertical
C16, C17, C18, C22: 1uF; C_0603_1608Metric
C19, C23, C35: 10uF; C_0805_2012Metric
C20: 2.2pF; C_0402_1005Metric
C21: 15uF; C_1206_3216Metric
D2: LED_Small; LED_0603_1608Metric
L1: 1uH; L_0805_2012Metric
L2: 3.3uH; L_1210_3225Metric
R11: 100m; R_0402_1005Metric
R12, R13: 10k; R_0402_1005Metric
R14: 649k; R_0402_1005Metric
R15: 294k; R_0402_1005Metric
R16: 600; R_0402_1005Metric
R17, R20: 100k; R_0402_1005Metric
R18: 113k; R_0402_1005Metric
R19: 0; R_0402_1005Metric
R23: 6.8k; R_0402_1005Metric
TP3: TestPoint; TestPoint_Pad_D1.0mm
U5: MIC5504-3.3YM5; SOT-23-5
U6: LM66200DRLR; SOT-5X3_DRL_TEX
U7: LM66100DCKR; SOT-363_SC-70-6
U8: LTC4065EDC-TRMPBF; DFN-6_DC_LIT
U11: LTC3306CACBZ-R7; CB-6-19_ADI

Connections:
+1V8: C21.1, L2.2, R11.2, R20.2, U6.6 (VIN2)
+3V3: C17.1, R12.1, U5.5 (VOUT), U6.3 (VIN1)
+BATT: BT1.1 (+), C19.1, R14.1, U8.3 (BAT), U11.C2 (VIN)
GND: BT1.2 (-), C16.2, C17.2, C18.2, C19.2, C21.2, C23.2, C35.2, R17.2, R18.2, R19.2, R23.2, U5.2 (GND), U6.1 (GND), U6.4 (ON), U6.5 (GND), U7.2 (GND), U8.1 (GND), U8.5 (~EN), U8.7 (EPAD), U11.A2 (GND); also elsewhere on the board
unnamed: C20.1, C23.1, C35.1, L1.2, L2.1, R11.1, R15.1
unnamed: C22.2, R19.1
unnamed: D2.2 (A), R16.2
unnamed: D2.1 (K), U8.2 (*CHRG)
unnamed: R12.2, U6.8 (ST)
unnamed: R13.2, U7.5 (ST)
unnamed: C22.1, R13.1, R16.1, U7.3 (~CE), U7.6 (Vout), U8.4 (VCC)
unnamed: R23.1, U8.6 (PROG)
unnamed: R14.2, R17.1, U11.B1 (EN)
unnamed: C20.2, R15.2, R18.1, U11.C1 (FB)
unnamed: R20.1, TP3.1, U11.A1 (PGOOD)
unnamed: L1.1, U11.B2 (SW)
VBUS: C16.1, C18.1, U5.1 (VIN), U5.3 (EN), U7.1 (Vin); also elsewhere on the board
VDD: U6.2 (VOUT), U6.7 (VOUT); also elsewhere on the board

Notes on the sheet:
Battery Charger
Ideal Diode OR
3.3V SMPS
1.8V SMPS

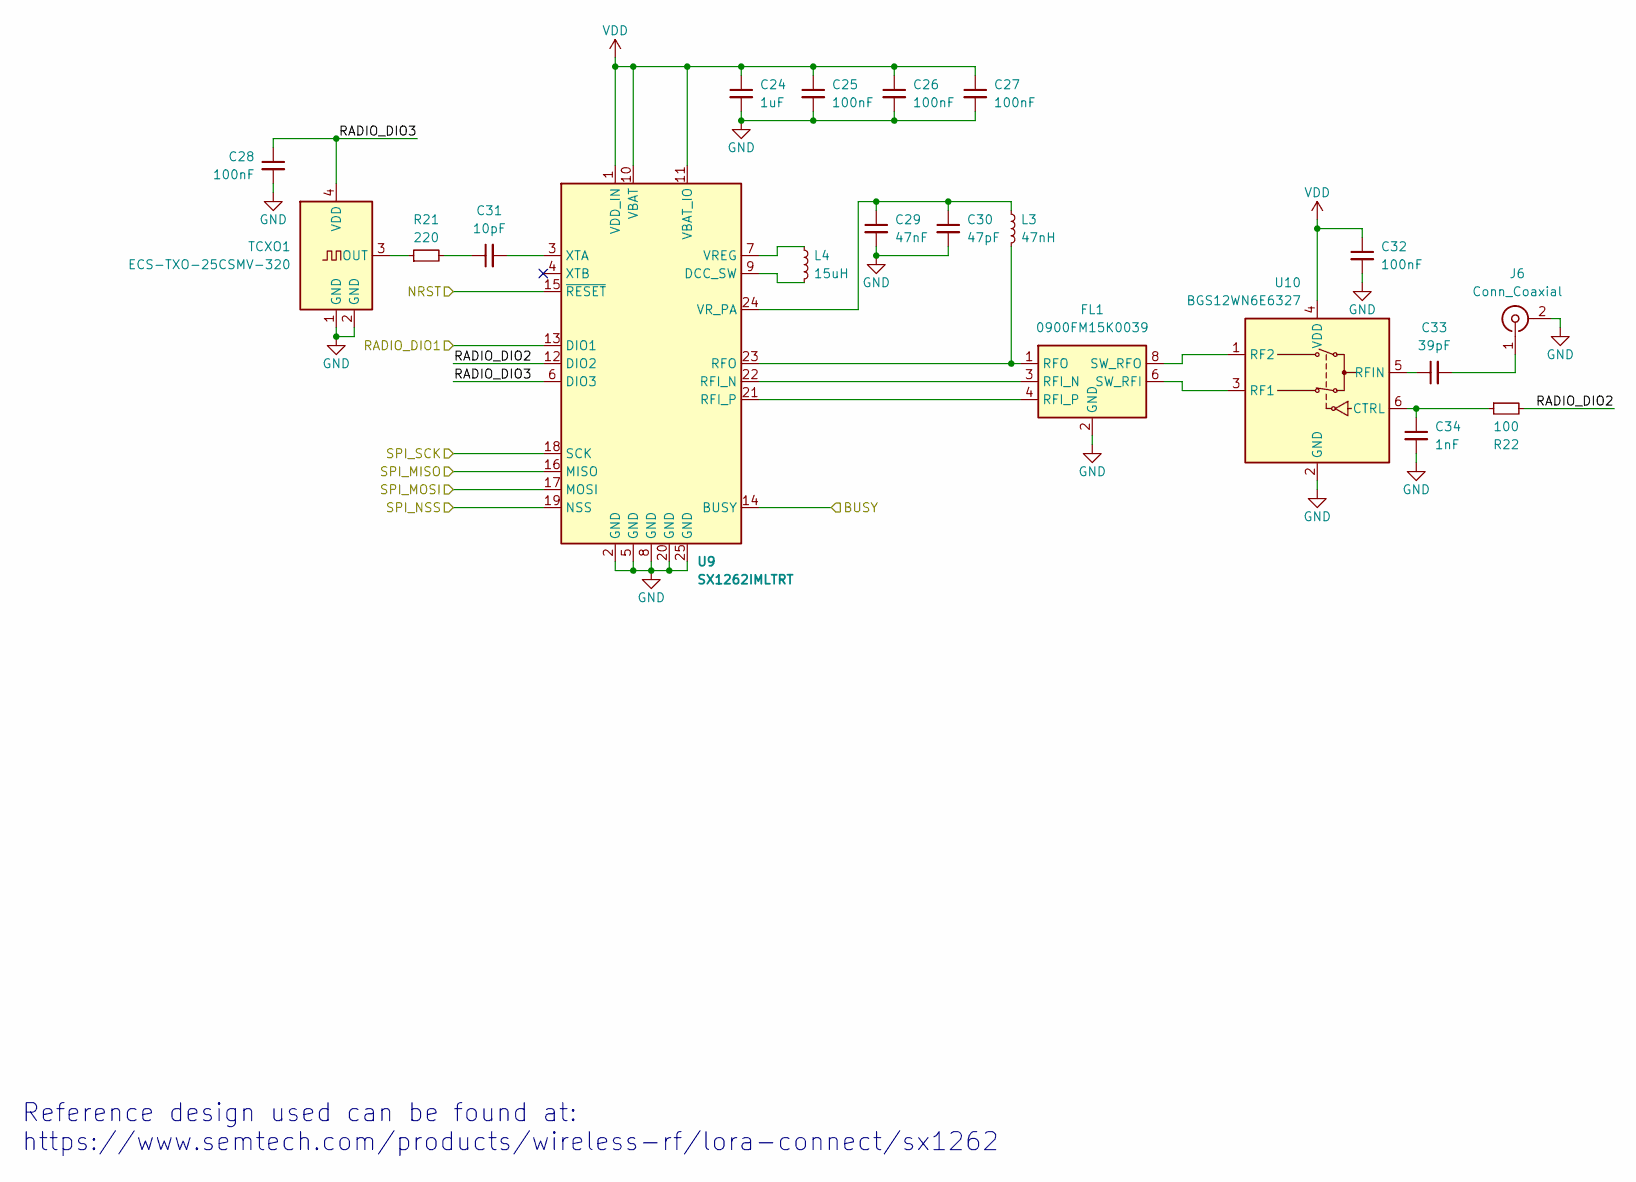
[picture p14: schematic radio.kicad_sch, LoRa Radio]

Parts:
C24: 1uF; C_0603_1608Metric
C25, C26, C27, C28, C32: 100nF; C_0402_1005Metric
C29: 47nF; C_0402_1005Metric
C30: 47pF; C_0402_1005Metric
C31: 10pF; C_0402_1005Metric
C33: 39pF; C_0402_1005Metric
C34: 1nF; C_0402_1005Metric
FL1: 0900FM15K0039; Balun_Johanson_0900FM15K0039
J6: Conn_Coaxial; U.FL_Molex_MCRF_73412-0110_Vertical
L3: 47nH; L_0402_1005Metric
L4: 15uH; L_0805_2012Metric
R21: 220; R_0402_1005Metric
R22: 100; R_0402_1005Metric
TCXO1: ECS-TXO-25CSMV-320; Crystal_SMD_2520-4Pin_2.5x2.0mm
U9: SX1262IMLTRT; QFN-24-1EP_4x4mm_P0.5mm_EP2.6x2.6mm
U10: BGS12WN6E6327; Infineon_PG-TSNP-6-10_0.7x1.1mm_0.7x1.1mm_P0.4mm

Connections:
/LoRa Radio/RADIO_DIO2: R22.2, U9.12 (DIO2)
/LoRa Radio/RADIO_DIO3: C28.1, TCXO1.4 (VDD), U9.6 (DIO3)
/RADIO_BUSY: U9.14 (BUSY); also elsewhere on the board
/RADIO_DIO1: U9.13 (DIO1); also elsewhere on the board
/RADIO_NSS: U9.19 (NSS); also elsewhere on the board
/SPI1_MISO: U9.16 (MISO); also elsewhere on the board
/SPI1_MOSI: U9.17 (MOSI); also elsewhere on the board
/SPI1_SCK: U9.18 (SCK); also elsewhere on the board
/T_NRST: U9.15 (~RESET); also elsewhere on the board
GND: C24.2, C25.2, C26.2, C27.2, C28.2, C29.2, C30.2, C32.2, C34.2, FL1.2 (GND), FL1.5 (GND), FL1.7 (GND), FL1.9 (GND), FL1.10 (GND), J6.2 (Ext), TCXO1.1 (GND), TCXO1.2 (GND), U9.2 (GND), U9.5 (GND), U9.8 (GND), U9.20 (GND), U9.25 (GND), U10.2 (GND); also elsewhere on the board
unnamed: C31.1, R21.2
unnamed: FL1.3 (RFI_N), U9.22 (RFI_N)
unnamed: FL1.4 (RFI_P), U9.21 (RFI_P)
unnamed: FL1.1 (RFO), L3.2, U9.23 (RFO)
unnamed: FL1.6 (SW_RFI), U10.3 (RF1)
unnamed: FL1.8 (SW_RFO), U10.1 (RF2)
unnamed: C33.2, J6.1 (In)
unnamed: R21.1, TCXO1.3 (OUT)
unnamed: L4.2, U9.9 (DCC_SW)
unnamed: L4.1, U9.7 (VREG)
unnamed: C29.1, C30.1, L3.1, U9.24 (VR_PA)
unnamed: C31.2, U9.3 (XTA)
unnamed: C34.1, R22.1, U10.6 (CTRL)
unnamed: C33.1, U10.5 (RFIN)
VDD: C24.1, C25.1, C26.1, C27.1, C32.1, U9.1 (VDD_IN), U9.10 (VBAT), U9.11 (VBAT_IO), U10.4 (VDD); also elsewhere on the board

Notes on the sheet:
Reference design used can be found at: https://www.semtech.com/products/wireless-rf/lora-connect/sx1262

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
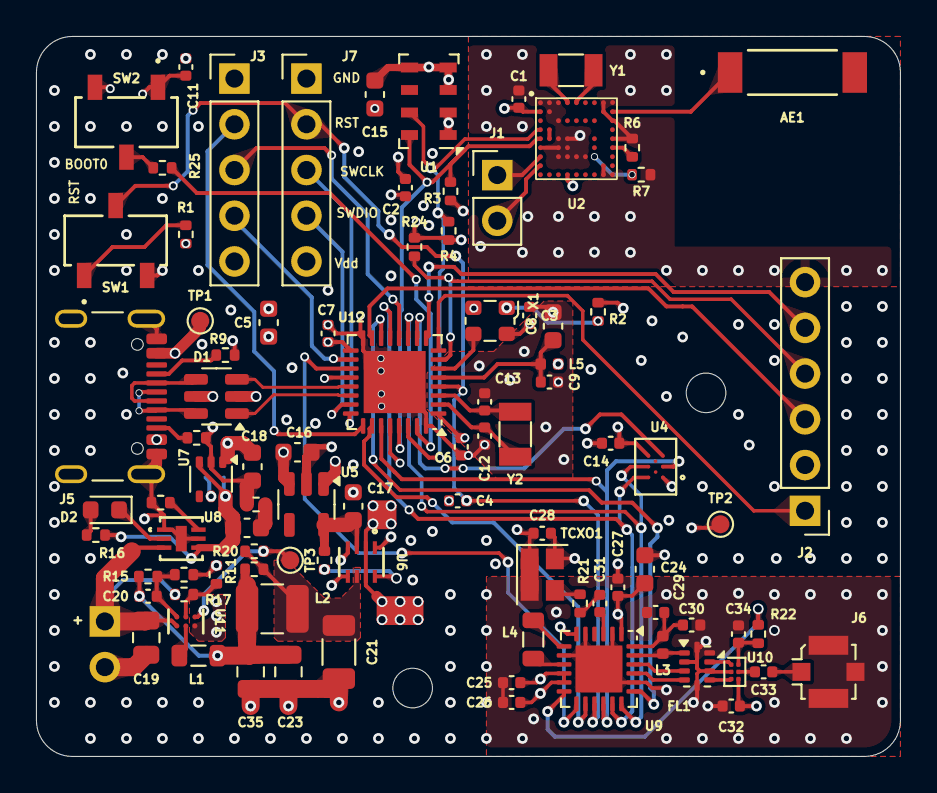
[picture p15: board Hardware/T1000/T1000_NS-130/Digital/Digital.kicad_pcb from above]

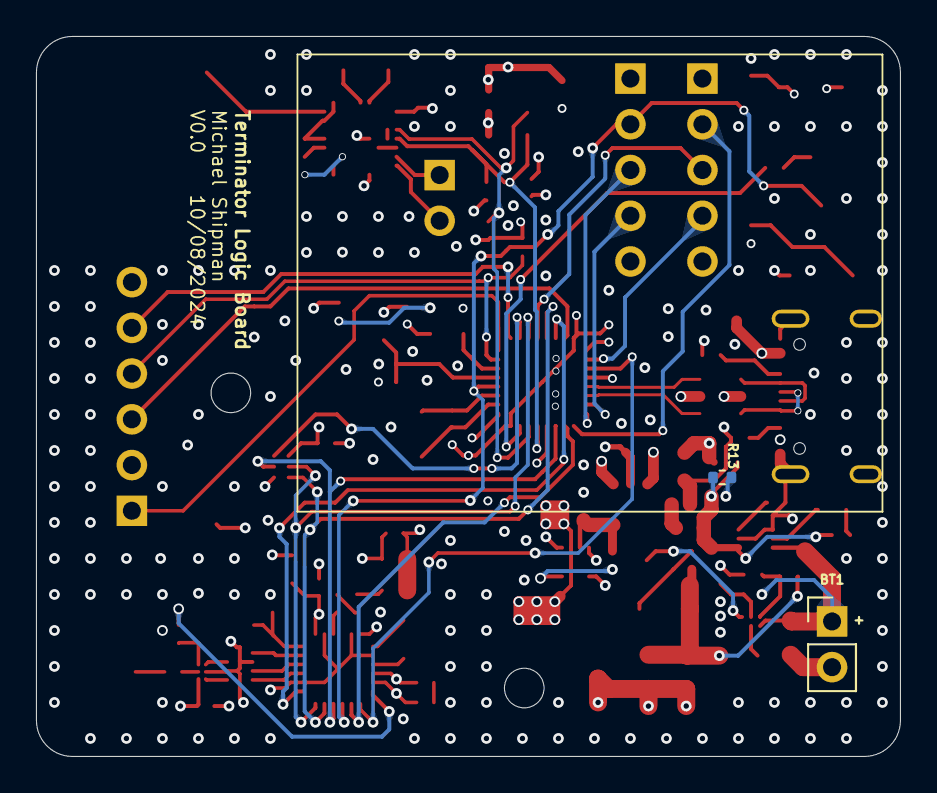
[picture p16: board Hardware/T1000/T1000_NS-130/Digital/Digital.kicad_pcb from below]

Board: 6 copper layers, 48.0 x 40.0 mm, 95 parts (2 on the bottom side), 76 nets.

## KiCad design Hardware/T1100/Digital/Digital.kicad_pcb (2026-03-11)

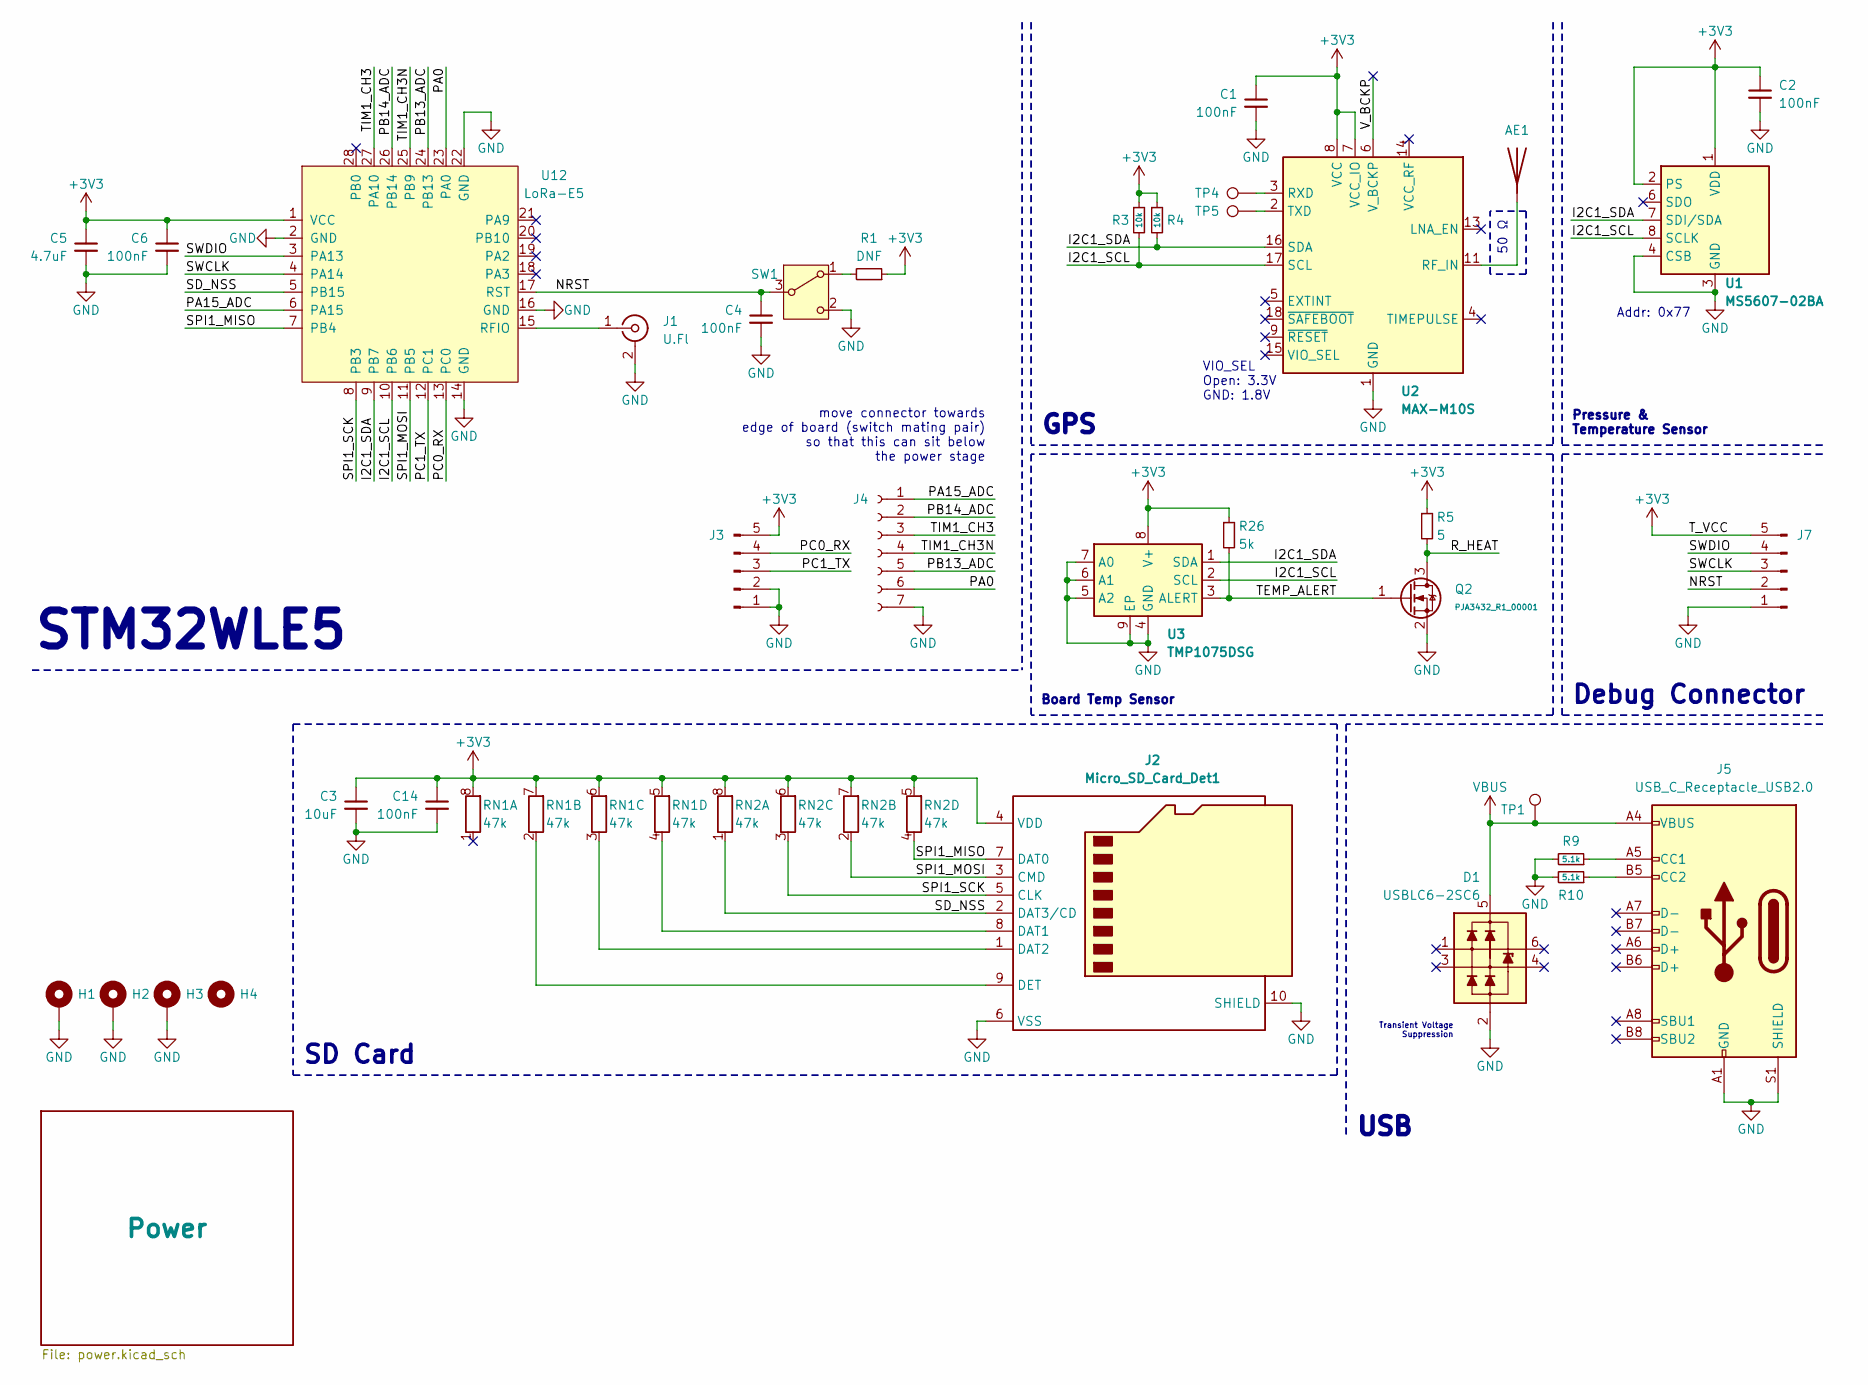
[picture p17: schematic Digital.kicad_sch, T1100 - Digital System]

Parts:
AE1: Antenna; ANT_1575AT_JOT-M
C1, C2, C4, C6, C14: 100nF; C_0402_1005Metric
C3: 10uF; C_0603_1608Metric
C5: 4.7uF; C_0603_1608Metric
D1: USBLC6-2SC6; TSOT-23-6
H1, H2, H3: MountingHole_Pad; Mounting_Wuerth_WA-SMSI-M2_H2mm_9774020243
H4: MountingHole; MountingHole_2.2mm_M2_DIN965
J1: U.Fl; U.FL_Molex_MCRF_73412-0110_Vertical
J2: Micro_SD_Card_Det1; microSD_HC_Molex_104031-0811
J3, J7: Conn_01x05_Pin; PinHeader_1x05_P2.54mm_Vertical
J4: Conn_01x07_Socket; Molex_ 1718570007
J5: USB_C_Receptacle_USB2.0; USB_C_Receptacle_GCT_USB4105-xx-A_16P_TopMnt_Horizontal
Q2: PJA3432_R1_00001; SOT-23
R1: DNF; R_0402_1005Metric
R3, R4: 10k; R_0402_1005Metric
R5: 5; R_0603_1608Metric
R9, R10: 5.1k; R_0402_1005Metric
R26: 5k; R_0402_1005Metric
RN1, RN2: 47k; R_Array_Convex_4x1206
SW1: SW_SPDT; CAS-120TB_NDC-M
TP1: TestPoint; TestPoint_Pad_D1.0mm
TP4, TP5: TestPoint; TestPoint_Pad_D3.0mm
U1: MS5607-02BA; LGA-8_3x5mm_P1.25mm
U2: MAX-M10S; ublox_MAX
U3: TMP1075DSG; WSON-8-1EP_2x2mm_P0.5mm_EP0.9x1.6mm_ThermalVias
U12: LoRa-E5

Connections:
+3V3: C1.1, C2.1, C3.1, C5.1, C6.1, C14.1, J2.4 (VDD), J3.5, J7.5, R1.1, R3.1, R4.1, R5.1, R26.1, RN1.5 (R4.2), RN1.6 (R3.2), RN1.7 (R2.2), RN1.8 (R1.2), RN2.5 (R4.2), RN2.6 (R3.2), RN2.7 (R2.2), RN2.8 (R1.2), U1.1 (VDD), U1.2 (PS), U2.7 (VCC_IO), U2.8 (VCC), U3.8 (V+), U12.1 (VCC); also elsewhere on the board
/I2C1_SCL: R3.2, U1.8 (SCLK), U2.17 (SCL), U3.2 (SCL), U12.10 (PB6)
/I2C1_SDA: R4.2, U1.7 (SDI/SDA), U2.16 (SDA), U3.1 (SDA), U12.9 (PB7)
/NRST: C4.1, J7.2, SW1.3 (C), U12.17 (RST)
/PA0: J4.6, U12.23 (PA0)
/PA15_ADC: J4.1, U12.6 (PA15)
/PB13_ADC: J4.5, U12.24 (PB13~)
/PB14_ADC: J4.2, U12.26 (PB14)
/PC0_RX: J3.4, U12.13 (PC0)
/PC1_TX: J3.3, U12.12 (PC1)
/R_HEAT: Q2.3 (D), R5.2
/SD_NSS: J2.2 (DAT3/CD), RN2.1 (R1.1), U12.5 (PB15)
/SPI1_MISO: J2.7 (DAT0), RN2.4 (R4.1), U12.7 (PB4)
/SPI1_MOSI: J2.3 (CMD), RN2.2 (R2.1), U12.11 (PB5)
/SPI1_SCK: J2.5 (CLK), RN2.3 (R3.1), U12.8 (PB3)
/SWCLK: J7.3, U12.4 (PA14)
/SWDIO: J7.4, U12.3 (PA13)
/TEMP_ALERT: Q2.1 (G), R26.2, U3.3 (ALERT)
/TIM1_CH3: J4.3, U12.27 (PA10)
/TIM1_CH3N: J4.4, U12.25 (PB9)
/V_BCKP: U2.6 (V_BCKP)
GND: C1.2, C2.2, C3.2, C4.2, C5.2, C6.2, C14.2, D1.2 (VN), H1.1, H2.1, H3.1, J1.2 (Ext), J2.6 (VSS), J2.10 (SHIELD), J3.1, J3.2, J4.7, J5.A1 (GND), J5.A12 (GND), J5.B1 (GND), J5.B12 (GND), J5.S1 (SHIELD), J7.1, Q2.2 (S), R9.2, R10.2, SW1.2 (B), U1.3 (GND), U1.4 (CSB), U1.5 (CSB), U2.1 (GND), U2.10 (GND), U2.12 (GND), U3.4 (GND), U3.5 (A2), U3.6 (A1), U3.7 (A0), U3.9 (EP), U12.2 (GND), U12.14 (GND), U12.16 (GND), U12.22 (GND); also elsewhere on the board
unnamed: AE1.1 (A), U2.11 (RF_IN)
unnamed: J1.1 (In), U12.15 (RFIO)
unnamed: J2.8 (DAT1), RN1.4 (R4.1)
unnamed: J2.1 (DAT2), RN1.3 (R3.1)
unnamed: J2.9 (DET), RN1.2 (R2.1)
unnamed: J5.A5 (CC1), R9.1
unnamed: J5.B5 (CC2), R10.1
unnamed: R1.2, SW1.1 (A)
unnamed: TP4.1, U2.3 (RXD)
unnamed: TP5.1, U2.2 (TXD)
VBUS: D1.5 (VP), J5.A4 (VBUS), J5.A9 (VBUS), J5.B4 (VBUS), J5.B9 (VBUS), TP1.1; also elsewhere on the board

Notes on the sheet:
GPS
Transient Voltage Suppression
Board Temp Sensor
VIO_SEL Open: 3.3V GND: 1.8V
Debug Connector
SD Card
50 Ω
USB
Pressure & Temperature Sensor
move connector towards edge of board (switch mating pair) so that this can sit below the power stage
STM32WLE5
Addr: 0x77

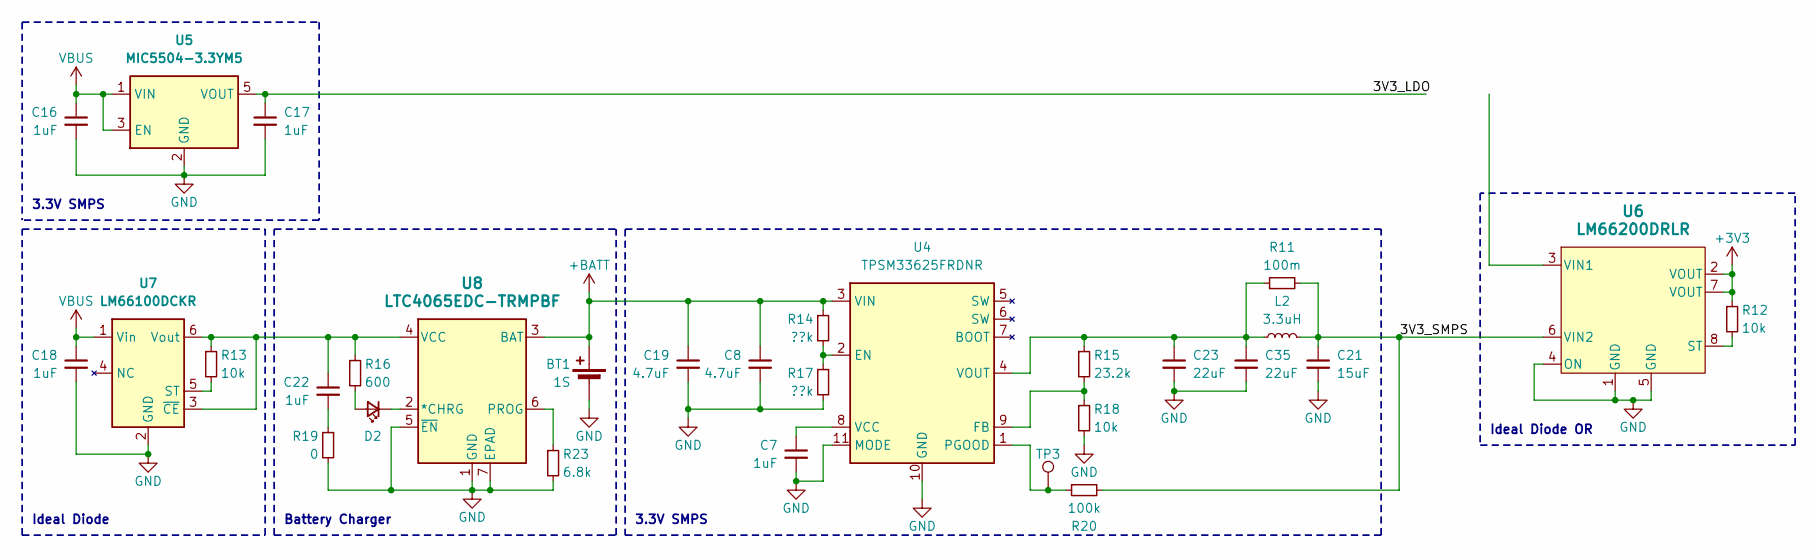
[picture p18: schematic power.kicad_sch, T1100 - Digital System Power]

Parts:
BT1: 1S; PinHeader_1x02_P2.54mm_Vertical
C7: 1uF; C_0402_1005Metric
C8, C19: 4.7uF; C_0805_2012Metric
C16, C17, C18, C22: 1uF; C_0603_1608Metric
C21: 15uF; C_1206_3216Metric
C23, C35: 22uF; C_0805_2012Metric
D2: LED_Small; LED_0603_1608Metric
L2: 3.3uH; L_1210_3225Metric
R11: 100m; R_0402_1005Metric
R12, R13, R18: 10k; R_0402_1005Metric
R14, R17: ??k; R_0402_1005Metric
R15: 23.2k; R_0402_1005Metric
R16: 600; R_0402_1005Metric
R19: 0; R_0402_1005Metric
R20: 100k; R_0402_1005Metric
R23: 6.8k; R_0402_1005Metric
TP3: TestPoint; TestPoint_Pad_D1.0mm
U4: TPSM33625FRDNR; RDN0011A-MFG-NO-VIA
U5: MIC5504-3.3YM5; SOT-23-5
U6: LM66200DRLR; SOT-5X3_DRL_TEX
U7: LM66100DCKR; SOT-363_SC-70-6
U8: LTC4065EDC-TRMPBF; DFN-6_DC_LIT

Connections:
+3V3: R12.1, U6.2 (VOUT), U6.7 (VOUT); also elsewhere on the board
+BATT: BT1.1 (+), C8.1, C19.1, R14.1, U4.3 (VIN), U8.3 (BAT)
/Power/3V3_LDO: C17.1, U5.5 (VOUT)
/Power/3V3_SMPS: C21.1, L2.2, R11.2, R20.2, U6.6 (VIN2)
GND: BT1.2 (-), C7.2, C8.2, C16.2, C17.2, C18.2, C19.2, C21.2, C23.2, C35.2, R17.2, R18.2, R19.2, R23.2, U4.10 (GND), U4.11 (MODE), U5.2 (GND), U6.1 (GND), U6.4 (ON), U6.5 (GND), U7.2 (GND), U8.1 (GND), U8.5 (~EN), U8.7 (EPAD); also elsewhere on the board
unnamed: C22.2, R19.1
unnamed: D2.2 (A), R16.2
unnamed: D2.1 (K), U8.2 (*CHRG)
unnamed: R14.2, R17.1, U4.2 (EN)
unnamed: R15.2, R18.1, U4.9 (FB)
unnamed: R20.1, TP3.1, U4.1 (PGOOD)
unnamed: C7.1, U4.8 (VCC)
unnamed: C23.1, C35.1, L2.1, R11.1, R15.1, U4.4 (VOUT)
unnamed: R12.2, U6.8 (ST)
unnamed: R13.2, U7.5 (ST)
unnamed: C22.1, R13.1, R16.1, U7.3 (~CE), U7.6 (Vout), U8.4 (VCC)
unnamed: R23.1, U8.6 (PROG)
VBUS: C16.1, C18.1, U5.1 (VIN), U5.3 (EN), U7.1 (Vin); also elsewhere on the board

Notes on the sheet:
Ideal Diode
Battery Charger
Ideal Diode OR
3.3V SMPS

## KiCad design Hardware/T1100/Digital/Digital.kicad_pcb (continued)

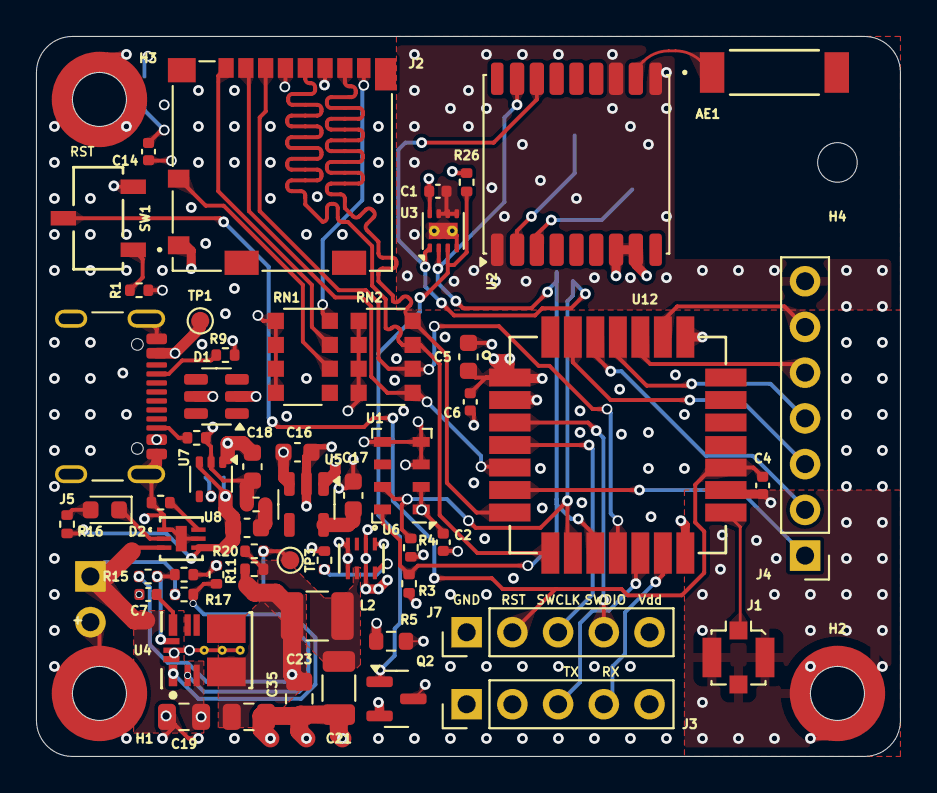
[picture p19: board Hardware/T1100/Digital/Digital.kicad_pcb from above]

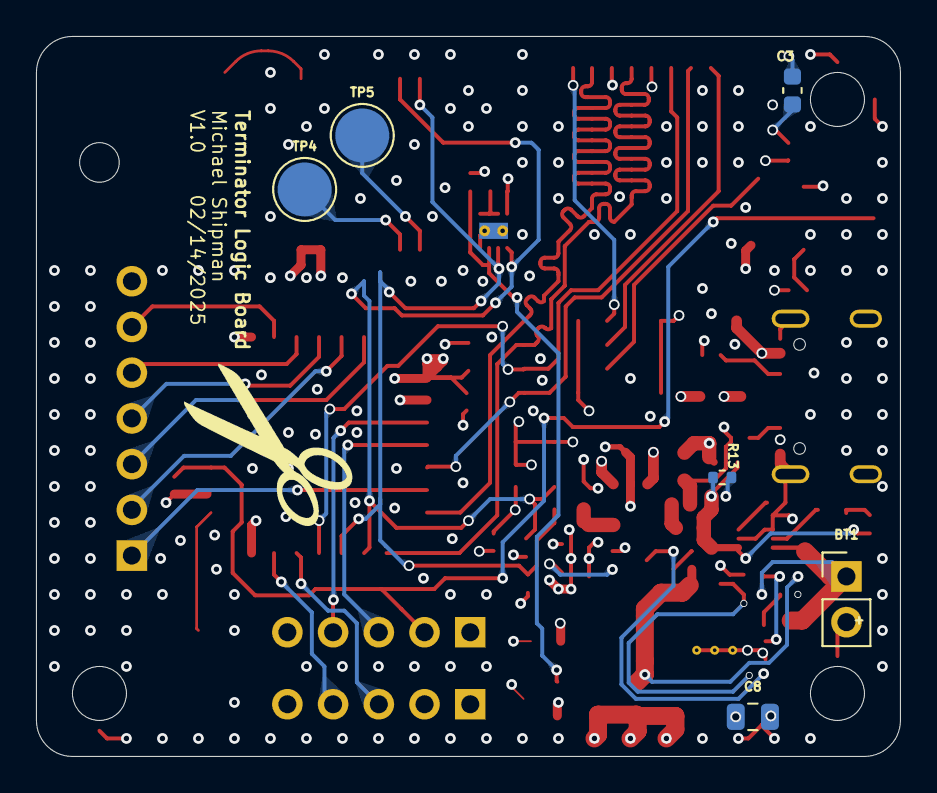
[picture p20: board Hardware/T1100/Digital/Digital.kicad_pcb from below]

Board: 6 copper layers, 48.0 x 40.0 mm, 67 parts (6 on the bottom side), 47 nets.

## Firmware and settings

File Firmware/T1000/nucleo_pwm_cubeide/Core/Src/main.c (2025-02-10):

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
/* Includes ------------------------------------------------------------------*/
#include "main.h"


void SystemClock_Config(void);
static void MX_GPIO_Init(void);
static void MX_TIM1_Init(void);
/**
  * @brief  The application entry point.
  * @retval int
  */
int main(void)
{

  /* MCU Configuration--------------------------------------------------------*/

  /* Reset of all peripherals, Initializes the Flash interface and the Systick. */
  LL_APB2_GRP1_EnableClock(LL_APB2_GRP1_PERIPH_SYSCFG);
  LL_APB1_GRP1_EnableClock(LL_APB1_GRP1_PERIPH_PWR);

  /* System interrupt init*/
  NVIC_SetPriorityGrouping(NVIC_PRIORITYGROUP_4);

  /* SysTick_IRQn interrupt configuration */
  NVIC_SetPriority(SysTick_IRQn, NVIC_EncodePriority(NVIC_GetPriorityGrouping(),15, 0));

  /* Configure the system clock */
  SystemClock_Config();

  /* Initialize all configured peripherals */
  MX_GPIO_Init();
  MX_TIM1_Init();
  /* Infinite loop */
  /* USER CODE BEGIN WHILE */
  LL_TIM_EnableCounter(TIM1);
  LL_TIM_CC_EnableChannel(TIM1, LL_TIM_CHANNEL_CH1N);
  LL_TIM_EnableAllOutputs(TIM1);
//  LL_TIM_GenerateEvent_UPDATE(TIM1);
//  LL_TIM_GenerateEvent_CC1(TIM1);
//  uint32_t counter_value = LL_TIM_GetCounter(TIM1);
  while (1)
  {
//	  LL_GPIO_SetOutputPin(GPIOB, LL_GPIO_PIN_13);



    LL_TIM_OC_SetCompareCH1(TIM1, 999);
    for (int i = 0; i < 100000; i++)
    	;
    LL_TIM_OC_SetCompareCH1(TIM1, 500);
    //for (int i = 0; i < 1000000; i++);
//    counter_value =  LL_TIM_GetCounter;

    LL_GPIO_ResetOutputPin(GPIOB, LL_GPIO_PIN_13);

    for (int i = 0; i < 100000; i++)
        	;

    /* USER CODE END WHILE */

    /* USER CODE BEGIN 3 */
  }
  /* USER CODE END 3 */
}

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


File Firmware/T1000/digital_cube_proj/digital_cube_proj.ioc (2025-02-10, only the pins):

Mcu.UserName=STM32L422KBUx
PA0-CK_IN.Signal=RCC_CK_IN
PA1.Signal=COMP1_INP
PA10.Signal=S_TIM1_CH3
PA2.Signal=ADCx_IN7
PA3.Signal=ADCx_IN8
PA4.Signal=GPIO_Output
PA5.Signal=SPI1_SCK
PA7.Signal=SPI1_MOSI
PA9.Signal=GPIO_Input
PB0.Signal=GPIO_Output
PB1.Signal=TIM1_CH3N
PB6.Signal=I2C1_SCL
PB7.Signal=I2C1_SDA

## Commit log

2023-07-31 init hardware
    [T1000.kicad_pcb, T1000.kicad_sch, power.kicad_sch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]
2023-07-31 added SD card
    [T1000.kicad_sch, power.kicad_sch, processor.kicad_sch]
2023-08-02 buck-boost initial implementation
    [T1000.kicad_pcb, power.kicad_sch]
2023-08-03 schematic updates
    [T1000.kicad_sch, power.kicad_sch]
2023-08-14 filter tuning
    [T1000.kicad_sch]
2023-09-11 started layout
    [T1000.kicad_pcb, T1000.kicad_sch]
2023-09-12 more layout
    [T1000.kicad_pcb, T1000.kicad_sch]
2023-09-13 little bit of routing, changed to MIA-M10 GPS to make my life harder
    [T1000.kicad_pcb, T1000.kicad_sch]
2023-09-13 bringing it together, also managed to crash Kicad so this commit can be considered under duress in a court of law
    [T1000.kicad_pcb, T1000.kicad_sch]
2024-09-06 created digital and RF combo board and did most of the layout
    [Digital.kicad_pcb, Digital.kicad_sch, T1000.kicad_pcb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]
2024-09-06 T1000 exports folder and schematic
2024-09-12 V0 changes before order
    [Digital-B_Cu.gbl, Digital-B_Mask.gbs, Digital-B_Paste.gbp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]
2024-09-19 basic cutdown power stage sim
2024-09-19 started working with LL drivers
2024-10-08 started STM32 package change (T1001)
    [Digital.kicad_pcb, Digital.kicad_sch]
2024-10-09 ordered T1001
    [Digital-B_Cu.gbl, Digital-B_Mask.gbs, Digital-B_Paste.gbp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]
2024-10-11 FRAM SPI device id read works
    [mkfs.xlsx]
2024-10-15 working PWM generation
2024-10-15 complemented PWM (sometimes need power reset?)
    [main.c]
2024-10-17 ADC test, works but not as well as needed
2024-10-22 created project for digital board
2024-10-22 helper functions and I2C
2024-10-29 V0.1 of cutdown board to add opamp scaling on current sense
    [cutdown-B_Cu.gbl, cutdown-B_Mask.gbs, cutdown-B_Paste.gbp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]
2024-10-29 copid rp2040 ms5607 driver in, still need to port I2C transactions
2024-10-31 added finicky MS5607 driver, not working right unsure if SW/HW
    [main.c]
2024-11-08 added a number of things but notably PID now that new power board is in, also GPS USART2 RX on PA15 header so that I can use an external GPS for now, all needs testing
2024-11-09 prelim PID is working, holding the current sense voltage at about the correct value, also added internal watchdog timer
    [main.c]
2024-11-18 code flown on NS-130
2024-11-23 optimizing PID loop, at 20.52 us right now
2024-11-23 boosted core clock to 80 MHz for PID testing, down to 6.4 us loop time as expected
2025-02-14 cutdown power stage V1.0 changes
    [cutdown.kicad_pcb, cutdown.kicad_sch]
2025-08-07 got radio to enter TX mode according to status/error flags, need to confirm with spectrum analyzer
    [main.c, t1100_ioc_test.ioc]
2025-08-09 code for NS-134, working TX and heater, sometimes working GPS (hardware issue)
    [main.c, stm32_helper.h, t1100_ioc_test.ioc]
2026-03-11 clean up and move and add T1100 stuff
    [Digital-B_Cu.gbl, Digital-B_Mask.gbs, Digital-B_Paste.gbp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]
2026-03-11 update kicad-lib
2026-03-11 T1000 NS-130 back up
    [Digital.kicad_pcb, Digital.kicad_sch, cutdown.kicad_pcb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]
2026-03-11 remove dupe directory
    [Digital.kicad_pcb, Digital.kicad_sch, cutdown.kicad_pcb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]

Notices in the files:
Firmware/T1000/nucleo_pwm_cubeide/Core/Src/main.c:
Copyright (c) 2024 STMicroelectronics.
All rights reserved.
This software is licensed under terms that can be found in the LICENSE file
